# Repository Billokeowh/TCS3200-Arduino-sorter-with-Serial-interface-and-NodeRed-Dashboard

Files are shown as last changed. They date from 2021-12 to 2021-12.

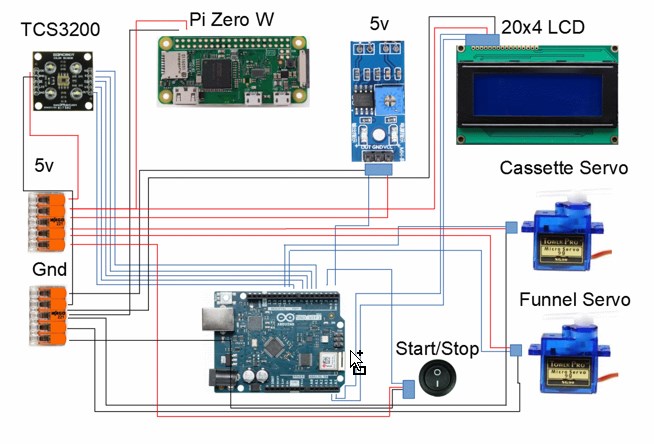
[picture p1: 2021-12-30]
Images/Wiring diagram.jpg

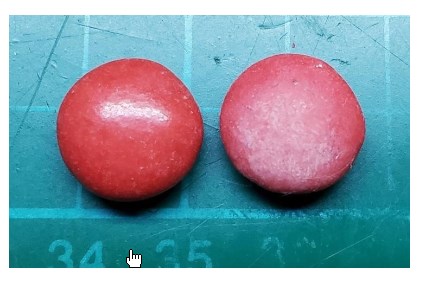
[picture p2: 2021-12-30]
Images/Moisture impact on M&Ms.jpg

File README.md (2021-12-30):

# TCS3200-Arduino-sorter-with-Serial-interface-and-NodeRed-Dashboard
Arduino TCS3200 based Colour sorter with Serial interface and  NodeRed Dashboard


- Carousel used to transport the sweets from the hopper to the Sensor. 

As a fun project I created an automated sorting machine that visually presents information to a user via an LCD and on-screen JavaScript dashboard. The machine is built from an Arduino Uno with a TCS3200 Colour sensor attached. M&M's/Smarties are loaded into a hopper and when the machine is started, it cycles through the contents of the hopper and sorts them by colour. The contents of the hopper are moved by a servo motor via a carousel to the TCS3200 colour sensor. This sensor determines what colour of sweet is in the read area and then passes it on to another servo. This servo then positions itself to move the detected sweet to the correct container. Once the sweet is distributed correctly, the cycle begins again. The amounts of each colour sorted as well as the status of the system are displayed on a 20x4 LCD display on the machine itself. Additionally, this information is sent via a serial connection to a PC running a software called Node-Red. This is a Javascript based program that ingests the information from the serial connection, displays it in the form of a dashboard on a computer monitor and also saves all information to a file in a csv format. The system has the ability to detect when the hopper is empty and alerts the operator of this fact. In addition to the colour sensor of the machine itself, there is also a Raspberry Pi zero W attached which can be used to remotely observe the machine from anywhere on the local network. This offers an additional method of quality assurance while running the machine. 


 - The Node-Red (JavaScript) dashboard used to display the received serial information. 

Node-Red is a development tool that is based on the Node.js Javascript runtime environment. It is a flow based visual programmer and it is what I elected to use to create a dashboard for a user to observe vital data about the machine and its processes. Node-Red is a service that must be started by entering the command prompt. Once running it can be accessed from your browser at http://127.0.0.1:1880/. Once started, it takes over all serial communication with the Arduino so the Arduino IDE’s port monitor no longer functions. The Arduino outputs a 15 character long string which contains all the relevant information about the machine. At this point Node-Red must be configured to ingest this string and present the relevant information correctly. To do this the “function” node is employed. The function node takes the 15 character string and dissects it into its relevant parts. For every piece of information that is required a different part of the string is used. In the example below the entire string is taken and is assigned to the value m. The string is then broken into pieces and in this case the 6th to the 9th characters are assigned to the variable “Green". We then output the green value and given that it is an integer we can use it to update charts, graphs and text boxes. This method is used to obtain the values of Red, Green and Blue and the same code is used only changing the output value to the relevant colour.


- How the String from the Arduino is parsed to get required values.

The Node-Red flow below is just a visual version of the json file that is attached above. To get this working on your machine you will have to make sure that Node-Red is running and the correct port numnber and baud rate is selected. Once up and running this connection is very stable and there were never any issues with it while I was testing. 



Any questions or suggestions would be most welcome.

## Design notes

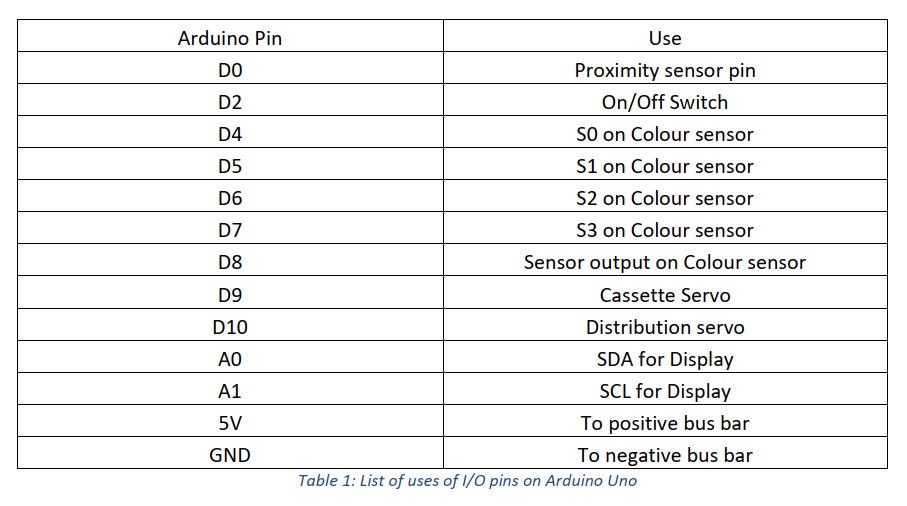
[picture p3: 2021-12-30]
Images/Arduino Pinout.jpg

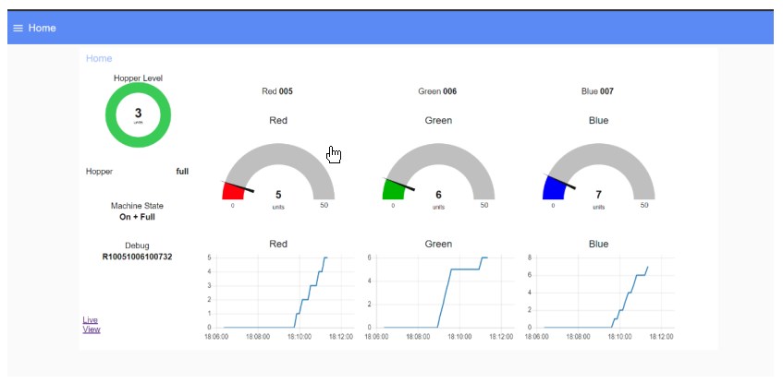
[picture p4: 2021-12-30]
Images/Node-Red dashboard.jpg

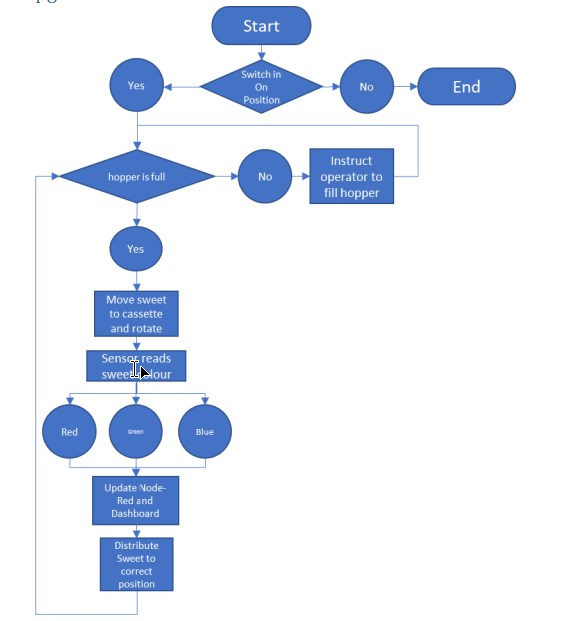
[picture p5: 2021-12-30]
Images/Flow chart.jpg

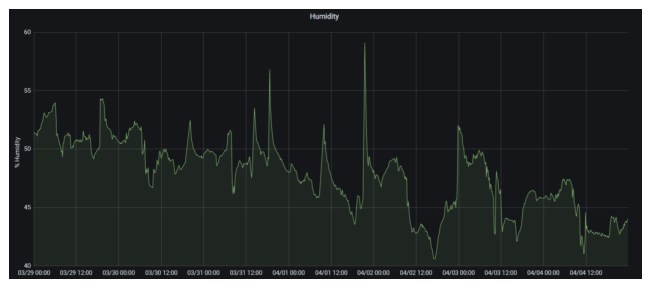
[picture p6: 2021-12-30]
Images/BME280 moiosture reading impact on M&M colour.jpg

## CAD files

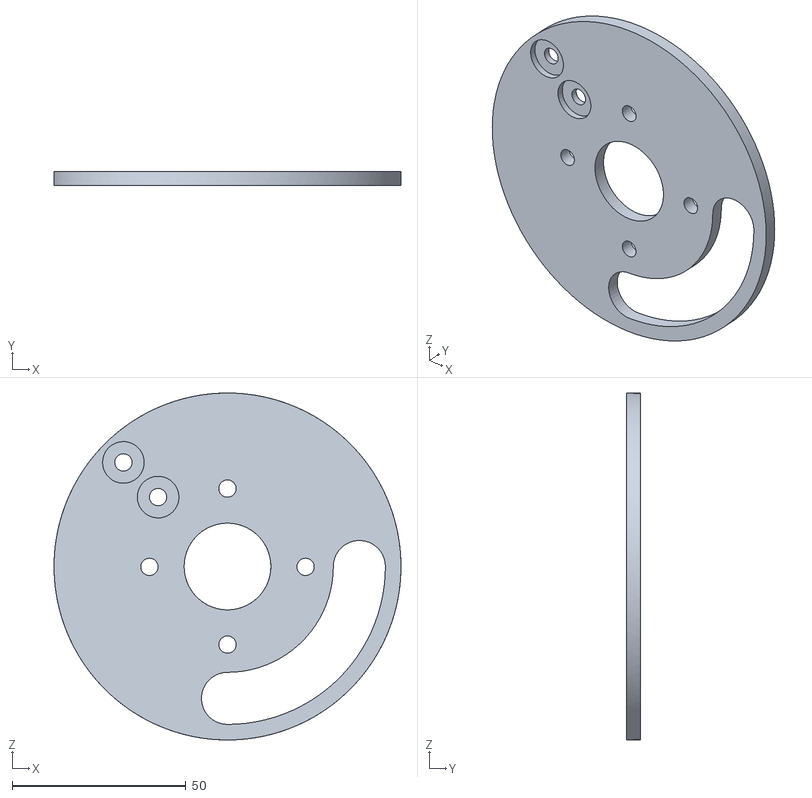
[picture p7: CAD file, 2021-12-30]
3D STL files/blocker plate sweets under cassette.stl
100.0 x 4.00 x 100.0

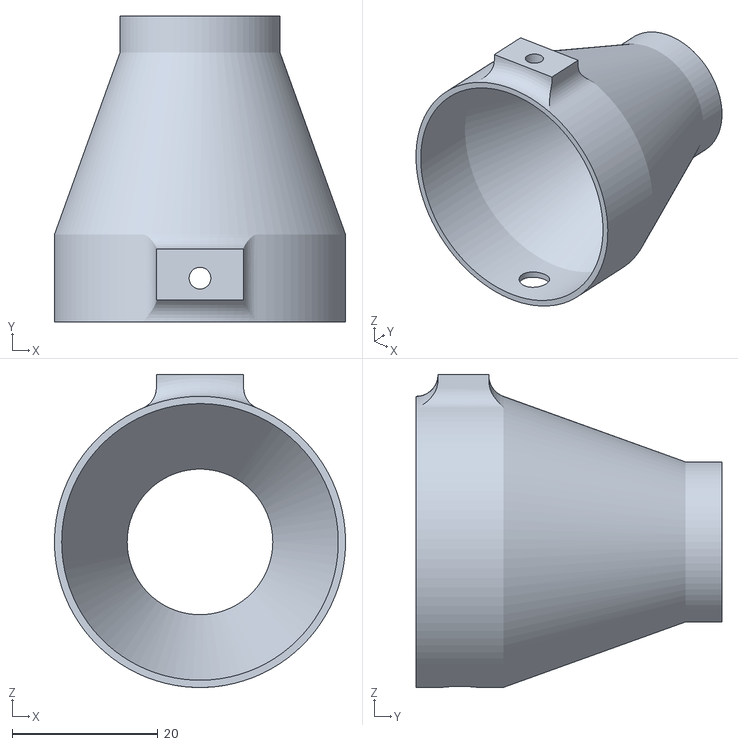
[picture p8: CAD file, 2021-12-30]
3D STL files/funnel piece for sweets.stl
40.0 x 42.0 x 43.0

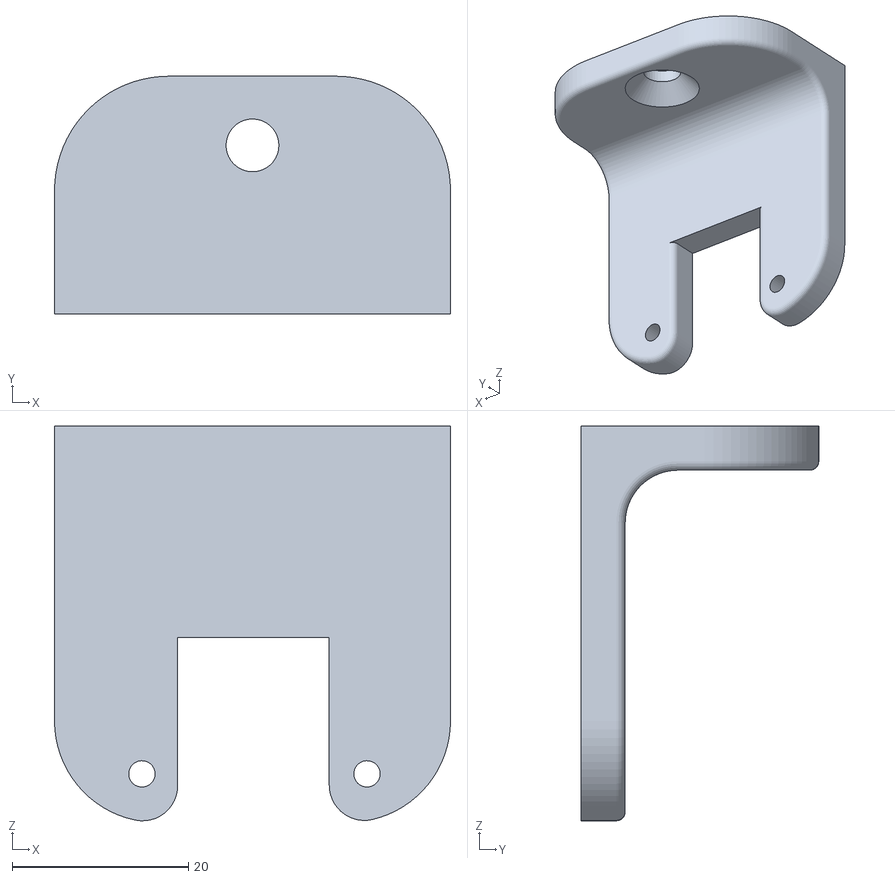
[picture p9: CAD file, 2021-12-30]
3D STL files/colour sensing unit support v1.stl
45.0 x 27.0 x 44.8

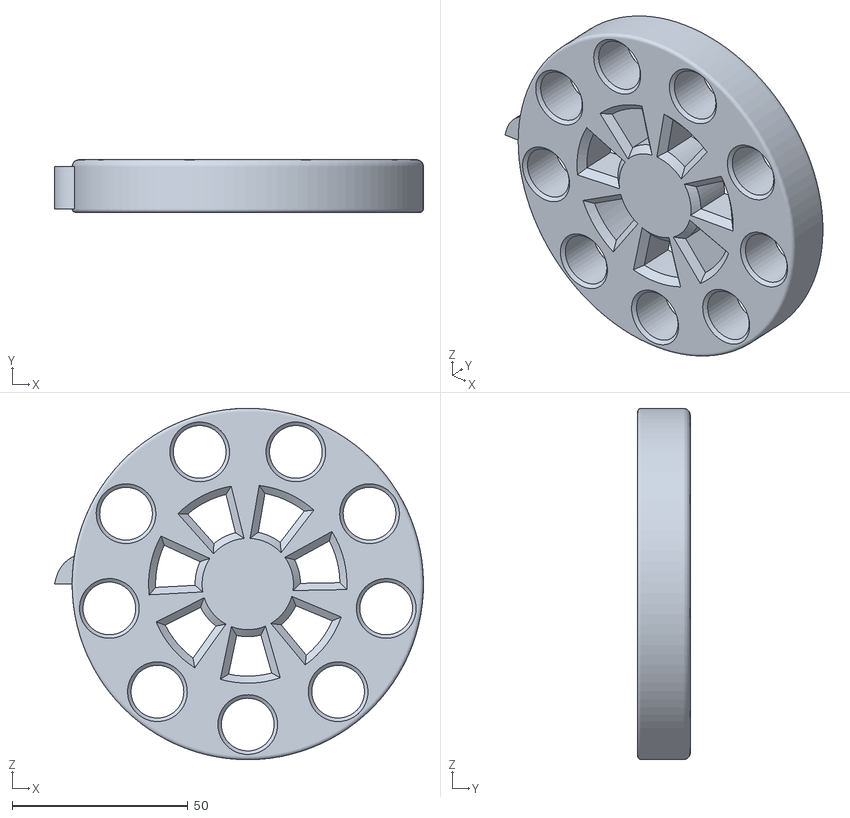
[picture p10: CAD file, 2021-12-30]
3D STL files/Sweet cassette peanuts.stl
105.0 x 15.0 x 100.0

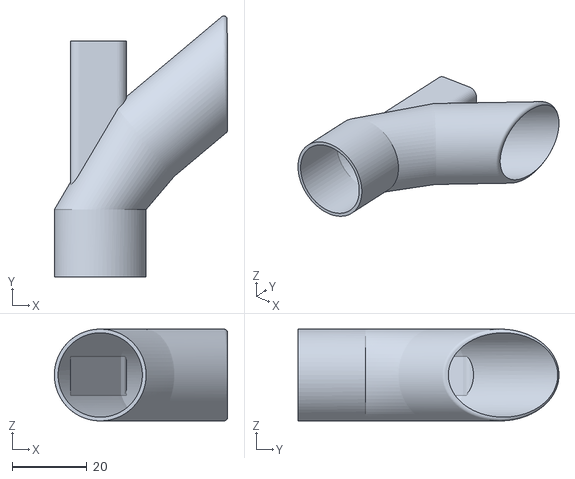
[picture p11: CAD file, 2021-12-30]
3D STL files/rotating-lower-funnel-piece.stl
46.2 x 69.6 x 24.5

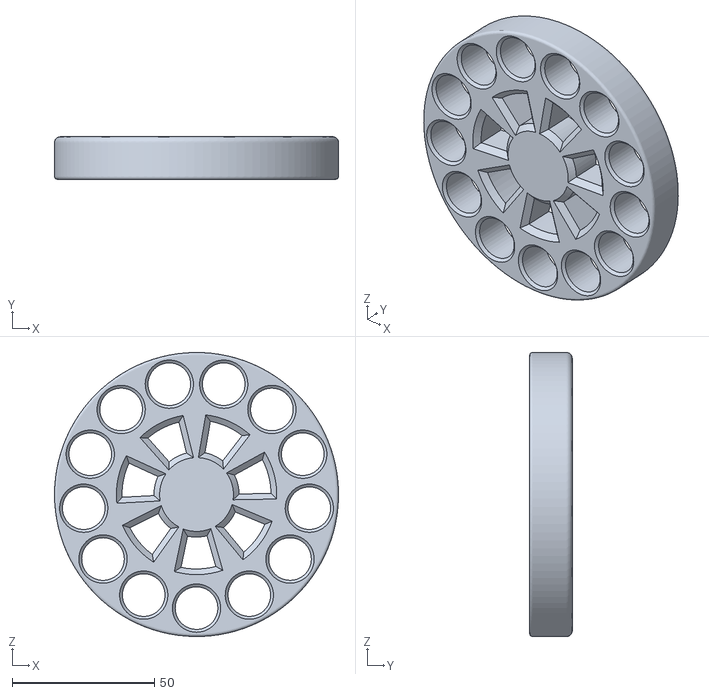
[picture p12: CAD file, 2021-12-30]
3D STL files/Sweet Cassette.stl
100.0 x 15.0 x 100.0

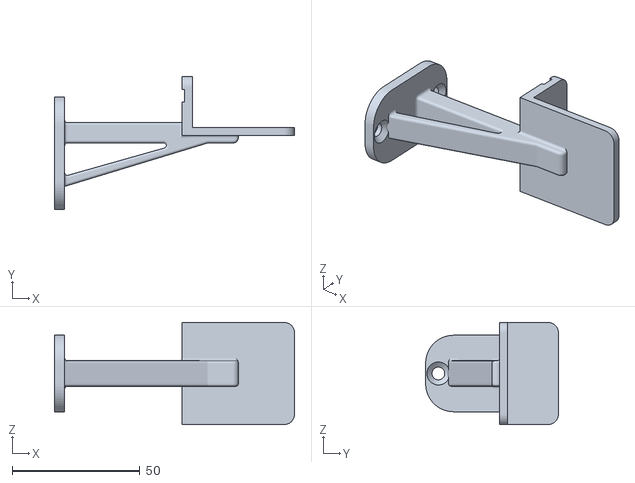
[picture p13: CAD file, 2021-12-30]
3D STL files/Sweet Cassette support.stl
94.0 x 52.0 x 40.0

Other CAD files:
3D STL files/sweet cassette smarties.stl

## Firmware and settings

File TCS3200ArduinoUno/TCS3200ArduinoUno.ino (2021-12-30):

#define S0 4
#define S1 5
#define S2 6
#define S3 7
#define sensorOut 8
#include <Servo.h>

#include <Wire.h>
#include <LiquidCrystal_I2C.h>

LiquidCrystal_I2C lcd(0x27, 20, 4);

Servo servocolour;
Servo servorotate;

int Redfrequency = 0;
int Bluefrequency = 0;
int Greenfrequency = 0; //Setting up integer to store Red, Green and Blue values in.
int angle = 0;          //Setting up integer to store angle values in.
int colourselection = 0;
int redtotal = 1000;
int greentotal = 1000;
int bluetotal = 1000; //Setting up integer to store Total Red, Green and Blue values in.
int sensorState = 0;  //Setting up integer for proximity sensor state
int hoppercounter = 0; //Setting up integer to store hopper level in.
int systemstate = 0;  //Setting up integer to store Machin Run/Not Run state.
int switchState = 0;  //Setting up integer to store switch state in.
const int buttonPin = 2;     // the number of the switch
const int ledPin =  13;      // the number of the LED pin

// variables will change:
int buttonState = 0;         // variable for reading the pushbutton status

void setup() {

  pinMode(ledPin, OUTPUT); // initialize the LED pin as an output:
  pinMode(buttonPin, INPUT);    // initialize the pushbutton pin as an input:
  Serial.begin(9600);
  pinMode(S0, OUTPUT);
  pinMode(S1, OUTPUT);
  pinMode(S2, OUTPUT);
  pinMode(S3, OUTPUT); // Setting all colour sensors as output devices.
  pinMode(0, INPUT);   // Setting Proximitiy sensor as an input
  pinMode(buttonPin, INPUT);  // Setting switch as an input
  pinMode(ledPin, OUTPUT);    // Setting LED as an output
  servocolour.attach(9);
  servorotate.attach(10);    // Defining Servo names and pins
  digitalWrite(S0, HIGH);
  digitalWrite(S1, LOW);     //Sets the output frequence scaling to 20%


  lcd.init();                      // initialize the lcd
  lcd.backlight();                  // initialize the backlight
  digitalWrite(0, LOW);             // initialize the priximity sensor in low state

}

void loop() {

  sensorState = digitalRead(0); // Check the hopper leve at the start of each loop

  if (sensorState == LOW) {           //If the sensor detects presence of sweet then set value to 3.
    hoppercounter = 3;
    delay(1000);
  }
  if ((sensorState == HIGH) && (hoppercounter >= 1))  { //If the sensor doesn't detects sweet and the hopper counter
    hoppercounter--;                                    // is still greater than zero then deduct 1 from hopper level each loop
    delay(1000);
  }



  buttonState = digitalRead(buttonPin);               // Read state of switch


  if (buttonState == HIGH) {        // check if the switch is on. If it is, the buttonState is HIGH + turn on LED.
    digitalWrite(ledPin, HIGH);


    //On AND EMPTY +++++++++++++++++++++++++++++++++++++++++++++++++++++++++++++++++++++++++++++++++++++++++++
    if  (hoppercounter == 0) {      // If there is nothing in hopper then tell the user via Serial and LCD
      lcd.clear();
      lcd.setCursor(0, 1);
      lcd.print("Sweet hopper");
      lcd.setCursor(0, 2);
      lcd.print("is empty");
      delay(1000);
      systemstate = 1;

    }

    //On AND FULL +++++++++++++++++++++++++++++++++++++++++++++++++++++++++++++++++++++++++++++++++++++++++++
    if  (hoppercounter > 0)  {                                // If switch is on and hopper is full then we can begin out sorting process


      //LOAD POSITION
      servorotate.write(140); //Servo to load position
      delay(200);
      servorotate.write(142); //Servo to load position
      delay(200);
      servorotate.write(144); //Servo to load position
      delay(200);
      // jiggle cassette to ensure sweet in cassette

      lcd.setCursor(0, 0);
      lcd.print("Load position");
      delay(1000);
      lcd.clear();
      //END OF LOADING                                        // Tell user sweet loaded via LCD.


      //CHECK POSITION
      servorotate.write(120); //Servo to check position
      delay(500);                                        // Servo to move sweet to camera view location


      lcd.setCursor(0, 0);
      lcd.print("Check position");
      delay(1000);
      lcd.clear();                                        // Tell user sweet is in check position via LCD.

      //READ POSITION
      servorotate.write(10);
      //Serial.println("Servo Set to read position");
      lcd.setCursor(0, 0);
      lcd.print("Read position");
      delay(500);                                        // Tell user sweet is in rad location via LCD.
      //END OF READ POSITION



      // Setting red filtered photodiodes to be read
      digitalWrite(S2, LOW);
      digitalWrite(S3, LOW);

      /* --------------RED COLOUR--------------*/

      // Reading the output frequency
      Redfrequency = pulseIn(sensorOut, LOW);
      Redfrequency = map(Redfrequency, 273, 279, 255, 0);
      Redfrequency = Redfrequency * (-1);        // Inverting output result
      delay(100);
      digitalWrite(S2, HIGH);                   // Setting Green filtered photodiodes to be read
      digitalWrite(S3, HIGH);

      /* --------------Green COLOUR--------------*/

      // Reading the output frequency
      Greenfrequency = pulseIn(sensorOut, LOW);
      Greenfrequency = map(Greenfrequency, 321, 328, 255, 0);
      Greenfrequency = Greenfrequency * (-1);
      delay(100);
      digitalWrite(S2, LOW);                     // Setting Blue filtered photodiodes to be read
      digitalWrite(S3, HIGH);

      /* --------------Blue COLOUR--------------*/

      // Reading the output frequency
      Bluefrequency = pulseIn(sensorOut, LOW);
      //Remaping the value of the frequency to the RGB Model of 0 to 255
      Bluefrequency = map(Bluefrequency, 268, 275, 255, 0);
      Bluefrequency = Bluefrequency * (-1);
      delay(100);

      /* Servo to load sweet into colour sensing chamber */
      delay(1000);

      //RED
      if ((Redfrequency < Bluefrequency) && (Redfrequency < Greenfrequency)) {
        //Serial.println("Red sweet");
        //Serial.println("Moving to Red");
        servocolour.write(0);
        lcd.setCursor(0, 1);
        lcd.print("Red");
        delay(500);
        lcd.clear();
        redtotal++;                                      //If redfrequency is the highest then its a red sweet and we increment red counter
        //and distribute to red servo position


      }

      //GREEN
      if ((Greenfrequency < Bluefrequency) && (Greenfrequency < Redfrequency)) {
        //Serial.println("Green sweet");
        //Serial.println("Moving to Green");
        servocolour.write(90);
        lcd.setCursor(0, 1);
        lcd.print("Green");
        delay(500);
        lcd.clear();
        greentotal++;                                   //If Greenfrequency is the highest then its a green sweet and we increment green counter
        //and distribute to green servo position


      }

      //BLUE
      if ((Bluefrequency < Redfrequency) && (Bluefrequency < Greenfrequency)) {
        //Serial.println("Blue sweet");
        //Serial.println("Moving to Blue");
        servocolour.write(180);
        lcd.setCursor(0, 1);
        lcd.print("Blue");
        delay(500);
        lcd.clear();
        bluetotal++;                                   //If Bluefrequency is the highest then its a blue sweet and we increment blue counter
        //and distribute to blue servo position

      }
      servorotate.write(0);
      delay(500);
      //Serial.println("Servo set to distribute position");
      lcd.setCursor(0, 0);
      lcd.print("Distribute position");
      lcd.clear();                                            // Tell user sweet is in distribute position via LCD.


      redtotal = redtotal - 1000;
      lcd.setCursor(0, 1);
      lcd.print("Red: ");
      lcd.setCursor(5, 1);
      lcd.print(redtotal);
      redtotal = redtotal + 1000;      // Format data correctly for displaying to LCD and then reformat bofore sendin to NodeRed via serial

      greentotal = greentotal - 1000;
      lcd.setCursor(0, 2);
      lcd.print("Green: ");
      lcd.setCursor(6, 2);
      lcd.print(greentotal);
      greentotal = greentotal + 1000;      // Format data correctly for displaying to LCD and then reformat bofore sendin to NodeRed via serial

      bluetotal = bluetotal - 1000;
      lcd.setCursor(0, 3);
      lcd.print("Blue: ");
      lcd.setCursor(5, 3);
      lcd.print(bluetotal);
      bluetotal = bluetotal + 1000;      // Format data correctly for displaying to LCD and then reformat bofre sendin to NodeRed via serial
      systemstate = 2;                   // Set system state
      delay(1000);

    }



  } else {
    // OFF AND EMPTY +++++++++++++++++++++++++++++++++++++++++++++++++++++++++++++++++++++++++++++++++++++++++++

    digitalWrite(ledPin, LOW);          // indicator LED off

    if (hoppercounter == 0)  {         // If the switch and th ehopper is empty is off then tell the user via Serial and LCD
      lcd.clear();
      lcd.setCursor(0, 0);
      lcd.print("Please switch the");
      lcd.setCursor(0, 1);
      lcd.print("Start switch");
      lcd.setCursor(0, 2);
      lcd.print("and fill hopper");
      delay(1000);
      //Serial.println("Off AND EMPTY");
      systemstate = 3;                   // Set system state

    }


    // OFF AND FULL +++++++++++++++++++++++++++++++++++++++++++++++++++++++++++++++++++++++++++++++++++++++++++

    if (hoppercounter > 0)   {                  // If the switch is off then tell the user via Serial and LCD
      lcd.clear();
      lcd.setCursor(0, 1);
      lcd.print("To run, move switch");
      lcd.setCursor(0, 2);
      lcd.print("to on position");
      delay(1000);
      //Serial.println("Off AND FULL");
      systemstate = 4;                        // Set system state

    }

  }

  Serial.print("R");
  Serial.print(redtotal);
  Serial.print(greentotal);
  Serial.print(bluetotal);
  Serial.print(hoppercounter);
  Serial.print(systemstate);             //Output the vital stats of the machine as one string.


  Serial.println("");                   // New string is always on new line
}

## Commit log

2021-12-30 Create TCS3200ArduinoUno.ino
    This is the main file for the Arduino Uno. This takes the value from the TCS3200 and then instructs the servos where to move the Sweet. In this configuration this sensor was quite reliable but do not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
2021-12-30 Add files via upload
    This is the wiring diagram showing how to connect all components.
2021-12-30 Add files via upload
    All STL Files for building main body of the machine
    [Sweet Cassette support.stl, Sweet Cassette.stl, Sweet cassteet peanuts.stl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]
2021-12-30 Add files via upload
    Flow chart showing operation of sorter.
2021-12-30 Add files via upload
    Arduino Pinout
2021-12-30 Add files via upload
    Node-Red flow file - Can be imported directly into Node-Red.
2021-12-30 Add files via upload
    Flow chart showing operation of the sorter.
